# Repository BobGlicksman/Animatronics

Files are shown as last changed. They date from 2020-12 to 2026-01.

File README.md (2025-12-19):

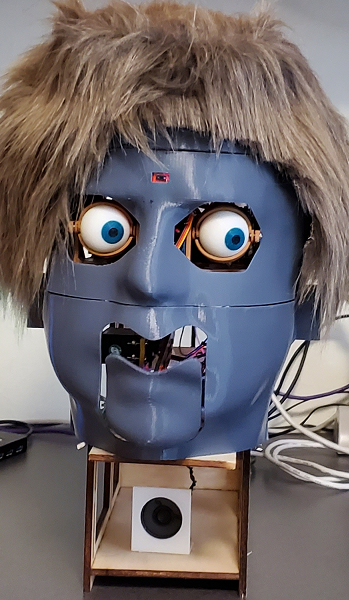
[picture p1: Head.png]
Head


# OVERVIEW.
This project developed an animatronic head.  The head is capable of detecting and tracking motion in its field of view and of controlling
an eye mechanism to "wake-up" and track this motion.  The head can also play various recorded voice clips and move its mouth to follow the 
audio in a "convincing manner".  The head can detect various events and select an appropriate voice clip to play in response to the event.

See the Overview document in the root folder of this repository for further details.

## Motivation.

This project was designed to explore various aspects of animatronics, including three specific technologies:

1. **TOF Sensor:**  The VL53L5CX intelligent sensor 
(https://www.sparkfun.com/sparkfun-qwiic-mini-tof-imager-vl53l5cx.html)
contains a matrix of SPAD diodes that detect the time-of-flight of infrared light
reflected off an object to compute the distance to that object.  The sensor can report out an 8 x 8 array of distance 
measurements up to 15 times per second, making it a "poor man's LIDAR".

2.  **Animatronic Eye Mechanism:**  We used an eye mechanism built from this project:
https://www.instructables.com/Simplified-3D-Printed-Animatronic-Dual-Eye-Mechani/ of Nilheim Mechatronics. 
They have a YouTube channel: https://goo.gl/7Cle6h. In June 2024, Will released a new version of the 3D files that 
snaps together - no screws! https://www.youtube.com/watch?v=uzPisRAmo2s.

3.  **Voice and Mouth Control:**  We use a DFPLayer Mini MP3 module from DFRobotics 
(https://www.dfrobot.com/product-1121.html?srsltid=AfmBOornrlH_d-dh73ndTnoJ0Bhm0fcPcsy0bjisI8v6idOF1iMq-ogo)
to play various audio clips that we recorded on a micro-SD card.  A custom-developed analog processing circuit
scales, filters and extracts the envelope from the audio signal and the sampled envelope undergoes further real-time
software digital signal processing in order to drive a mouth servo in a "convincing manner".

## R & D.

In order to best perform the R&D associated with this project, a laser cut skeleton was developed so that the electronics and servos
can be positioned flexibly.  The "head" itself is 3D printed and flexibly attached to the skeleton via 3D printed ears with magnets
glued onto the mounting ears and the head pieces.  All CAD files for the laser cut and 3D printed pieces are included in this repository.

### Eye Movement.

In order to explore using the complex eye mechanism to create realistic eye movement scenarios, a flexible software system was
developed.

1. **Scene:**  A "scene" is the combination of the movements of the 6 eye servos to produce some specific effect, e.g. blink the eyes.

2. **Scenario:**  A "scenario" is a timed script of various scenes that produce some overall effect, e.g. a "sleepy dog" whose eyes 
periodically open just a crack and the eyeballs move around to survey the landscape, and then the eyes close and the dog goes 
back to sleep.

Scenes and Scenarios can be easily custom-defined and combined to create a wide variety of overall eye motion effects.  In addition,
scenarios are defined and implemented to effect eye movement to realistically track motion detected by the TOF sensor.

### Voice and Mouth Movement.

The mouth control electronics can play pre-recorded MP3 voice clips under software command by the onboard microcontroller.
A custom-designed analog signal processing circuit provides the microcontroller's A/D converter with analog signals that 
it can sample and process digitally.

1. **Scaled audio:**  the left audio MP3 player channel is shifted and scaled to be within the microcontroller's A/D 
converter range of 0 - 3.3 volts.  The signal is also filtered to a 3.3 KHz bandwidth (telephone audio quality) so 
that the microcontroller can sample this signal at 8 KHz (> the Nyquist criteria) and perform whatever digital signal 
processing is desired (at 125 microseconds per sample).
The analog AC signal is offset for the single supply A/D converter and the zero-offset voltage is provided on another A/D converter input
so that this offset can be subtracted (in software) from each sample.  These inputs are provided by the hardware but are not used
in the currently released software.

2. **Envelope Extraction:**  The scaled audio signal is further processed to extract the "envelope" of the audio signal by AM demodulation.
The bandwidth of the extracted envelope signal is approximately 40 Hz, which was empirically determined to preserve the full
information about the vocal elements of the voice clip while rejecting the "carrier" frequencies.  The envelope signal is 
connected to a 3rd A/D converter channel and the software samples this at 100 Hz.

The sampled envelope signal is processed in software to control the mouth servo.  In order to explore the nuances of controlling
the mouth servo to be "convincing", various configurable processing stages are provided in the released software:

a. **Linear and non-linear processing:**  The input envelope samples are scaled using either a linear or a non-linear scaling
algorithm.  The released software is configured for linear scaling, but realistic non-linear algorithms may be explored in
the future.

b. **Averaging:**  The 40 Hz envelope bandwidth and 100 Hz sampling are currently used to drive the mouth servo.  However,
1 to 5 samples may be averaged before being mapped to the servo drive.  The servo that we are using seems to work best
when driven without averaging the samples, and extreme averaging creates a noticeable lag between the audio and mouth movements.
However, averaging may be useful with other mechanical mouth linkages.

c.  **Servo scaling:** the processed samples are scaled to the desired servo range of travel before being used to control the mouth
servo.

### TOF Sensor.

The TOF sensor is very sophisticated and required a substantial amount of experimentation before we could use it successfully.
After figuring out what all of the controllable parameters do and how best to set them, we then worked on the actual application
of the sensor to this project.  The application includes:

1.  **Calibrating the room:**  Upon powering up the head, the room should be empty.  The software records the distance measurements
for the empty room so that it can later determine if anything has entered the room and respond to it.

2.  **Tracking movement:**  Tracking movement within the sensor's field of view turned out to be a challenge, as an 8 x 8 matrix of
distance measurements is complex.  In order to fix a point in space that is closet to the sensor, we had to combine both
spatial and temporal filters to reject "noise" in the data.  This filtering was necessary to produce non-jittery positioning
of the eyes to focus on the closest subject area in space.

3.  **Event detection:**  The software further processes the TOF data in order to detect various "events" for the head to
respond to:  (a) person(s) entering the TOF field of view, (b) person(s) leaving the TOF field of view, (c) person(s)
coming too close to the head.  Other events might be explored in the future.

# WHAT IS IN THIS REPOSITORY.

## Top Level.

1.  This README file.

2.  A photo of the Head.

3.  An Overview document describing this project in more detail.

4.  License information.

## Data Folder.

This folder contains digitized audio test files that were used with analysis and circuit simulation software to develop the analog
signal processing parameters for the circuit design.  These files are preserved for historical purposes and for further research;
they are not needed to implement the current animatronic head design.

## Documents Folder.

This folder contains the documentation for this project including several documents that detail the design, construction and operation of this project.

## Hardware Folder.

This folder contains information about the electronic design, including PCB CAD files and hookup data

## Legacy Folder.

This folder contains source code for various test programs that were used to exercise and research the various components
of the animatronic head prior to integrating the complete project.  These files are not part of the released head design but
are retained for possible use in future R&D.

## Mechanical Folder.

This folder contains the 2D and 3D CAD files for the skeleton, the head, the eye mechanism and other 3D printed mechanical
components of this project.

## Software Folder.

This folder contains source code for the two Particle Photon 1 microcontrollers used on this project.  The source code includes
the released operational code for each of the Photons, as well as some test and calibration code that needs to be used for
construction and calibration of the animatronic head.

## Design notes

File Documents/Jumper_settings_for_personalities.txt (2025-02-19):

JUMPER SETTINGS FOR PERSONALITIES

A5 = MSB; A4 = LSB; Logic is positive (open pin = 1, grounded pin = 0

Bob Personality #1:  ground both A4 and A5
Bob Personality #2 (not yet implemented): Ground A5, Open A4
Jim Personality #1: Open A5, Ground A4
Jim Personality #2 (not yet implemented): Open A5, Open A4

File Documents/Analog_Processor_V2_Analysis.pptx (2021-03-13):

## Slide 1

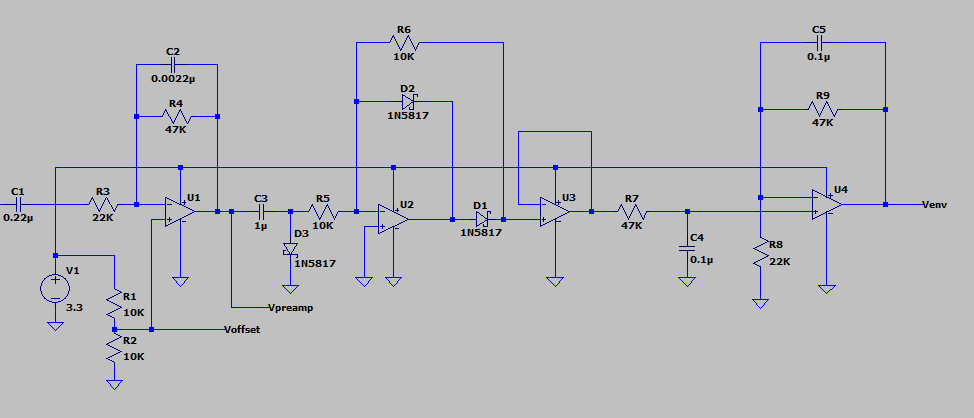
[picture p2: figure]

Op-Amps are OPA4342
- Quad opamp
- Single Supply
- Rail-Rail
- FET

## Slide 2

Input Filter/Preamp

Rectifier

Vpreamp

Voffset

Buffer

Envelope Filter

Audio
Input

Venv

Env Filter:
- Envelope filter (~0Hz – 40Hz)
- ~ 2x Gain

Pre-amp:
- Audio filter (~3Hz – 3KHz)
- DC offset (50% Vsupply)
- ~2x Gain

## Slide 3

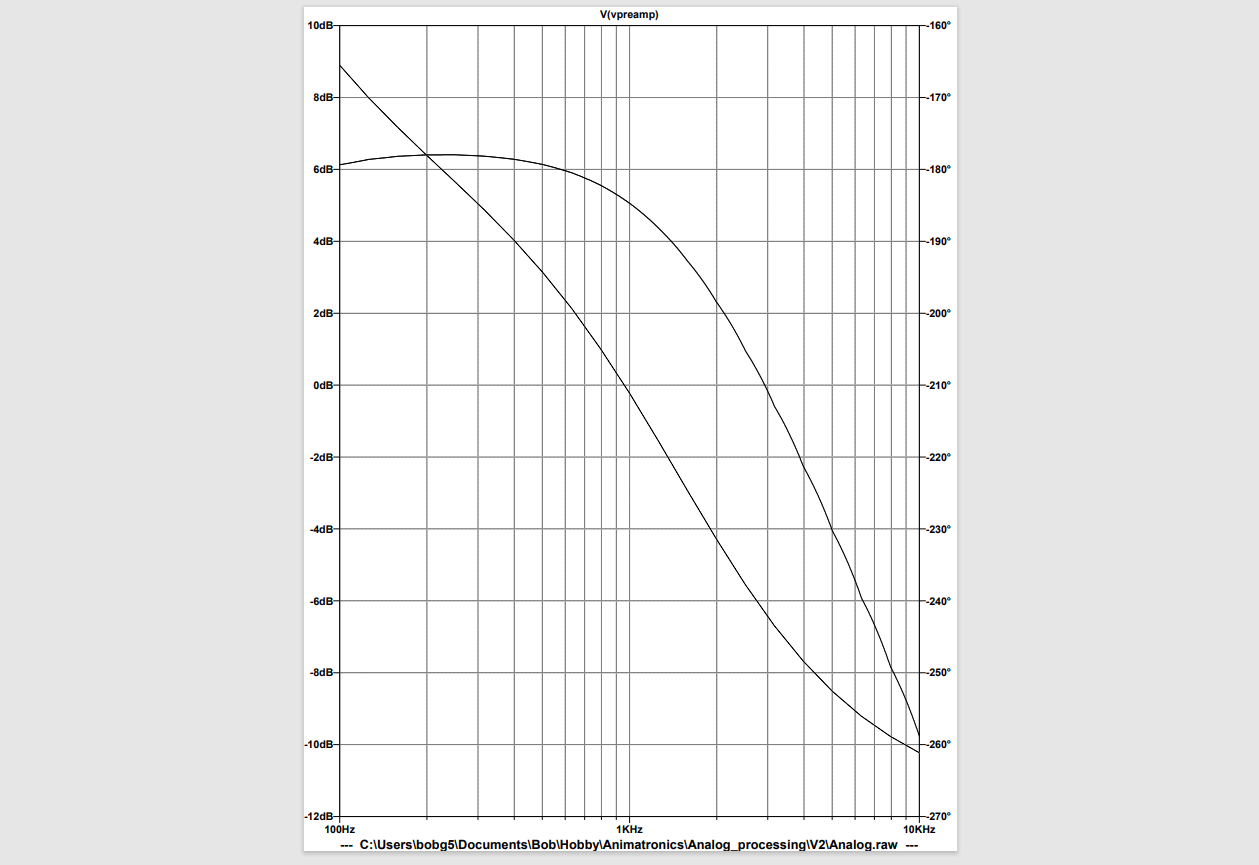
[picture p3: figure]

Frequency

Phase

Preamplifier
Frequency Response

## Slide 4

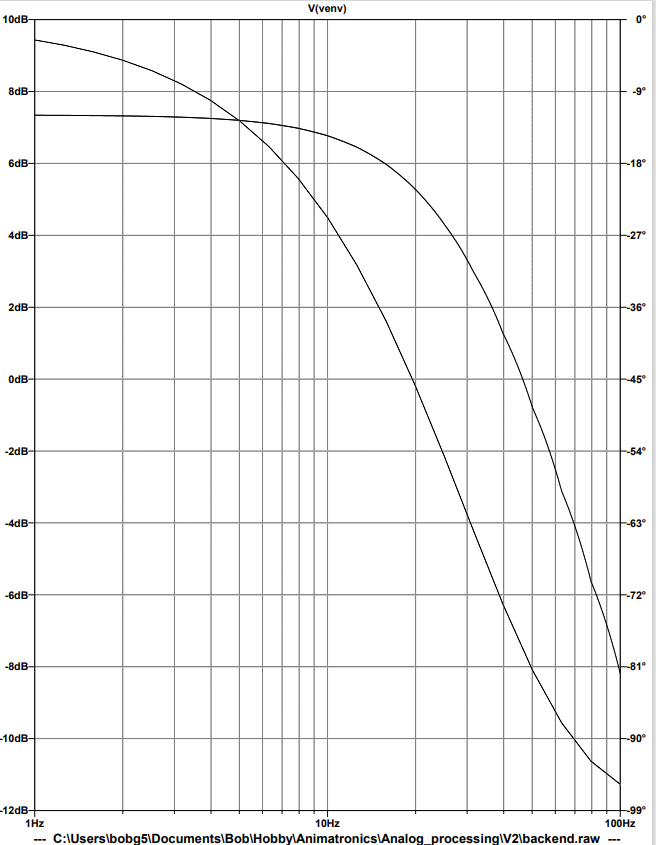
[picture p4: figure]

Frequency

Envelope Filter
Frequency Response

Phase

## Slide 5

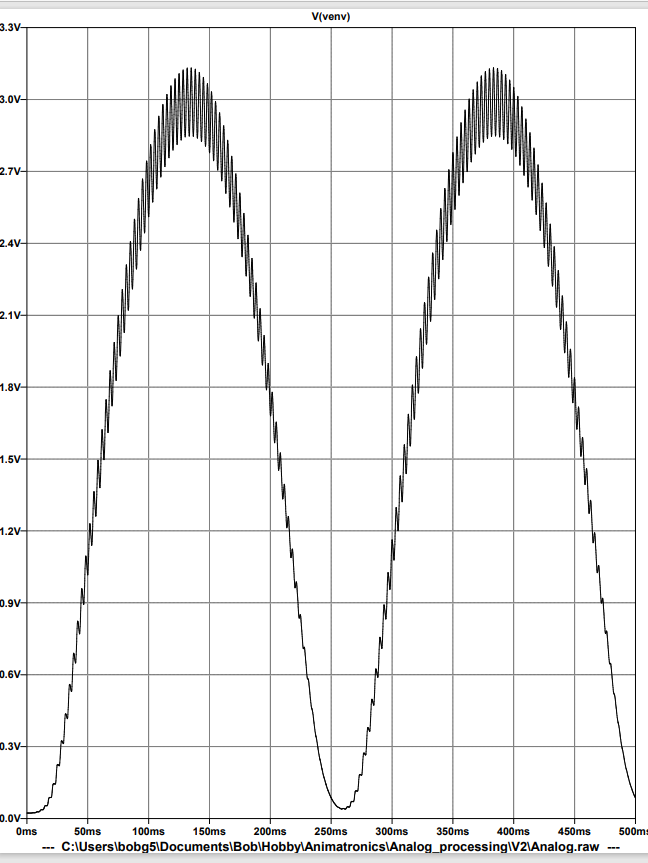
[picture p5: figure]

Carrier = 300 Hz
Modulation = 2 Hz

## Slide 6

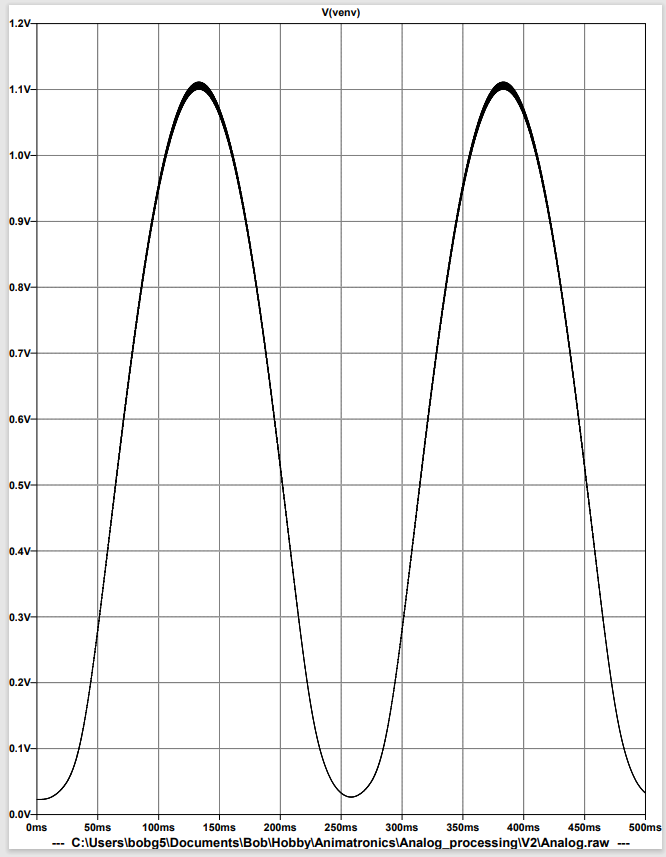
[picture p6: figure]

Carrier = 3000 Hz
Modulation = 2 Hz

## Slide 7

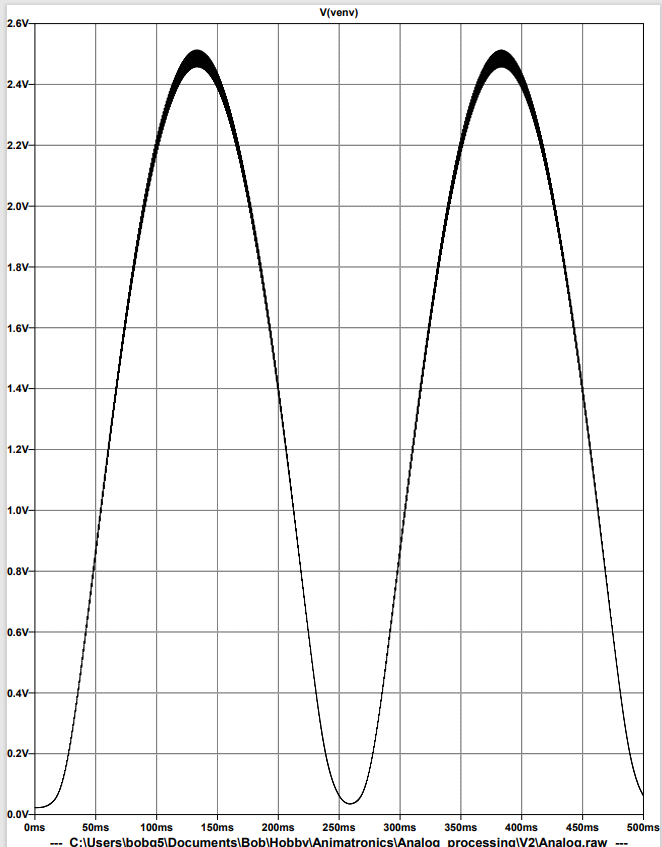
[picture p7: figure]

Carrier = 1200 Hz
Modulation = 2 Hz

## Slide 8

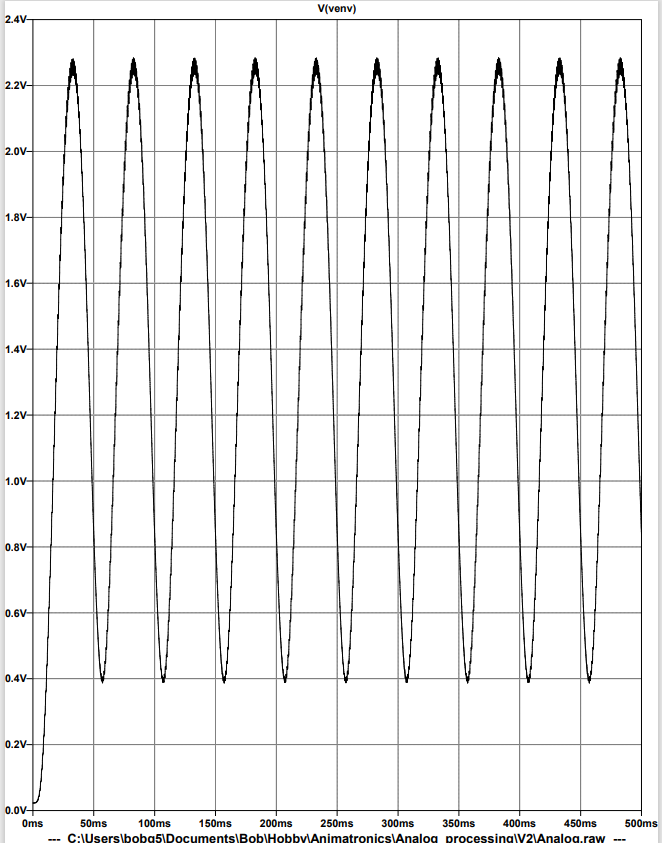
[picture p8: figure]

Carrier = 1200 Hz
Modulation = 10 Hz

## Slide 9

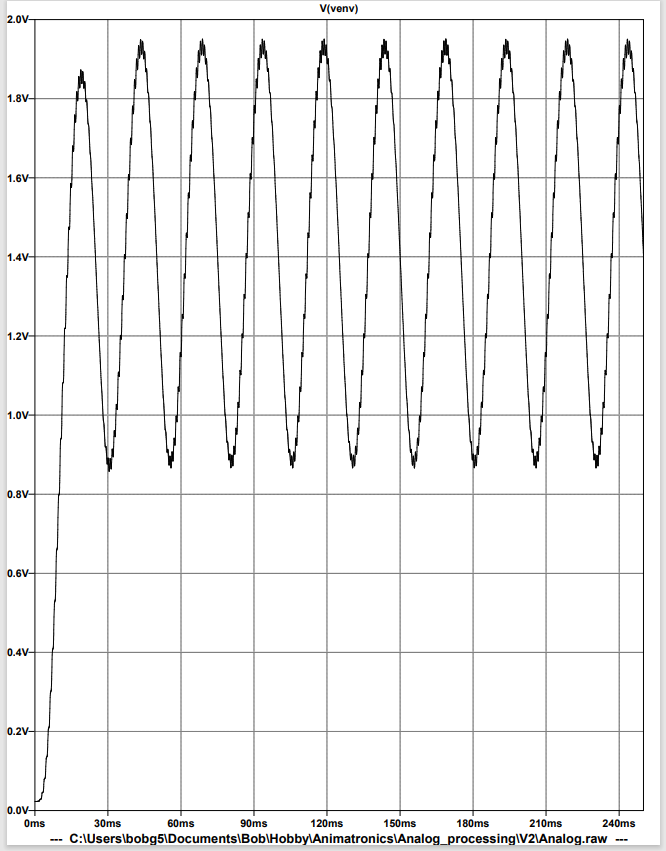
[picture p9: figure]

Carrier = 1200 Hz
Modulation = 20 Hz

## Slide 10

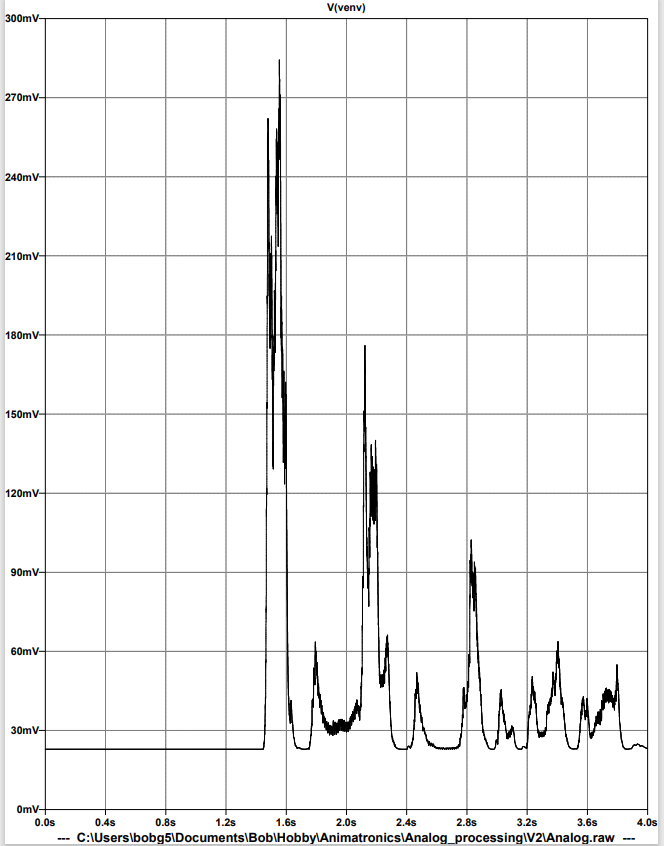
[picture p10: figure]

Welcome.wav

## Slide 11

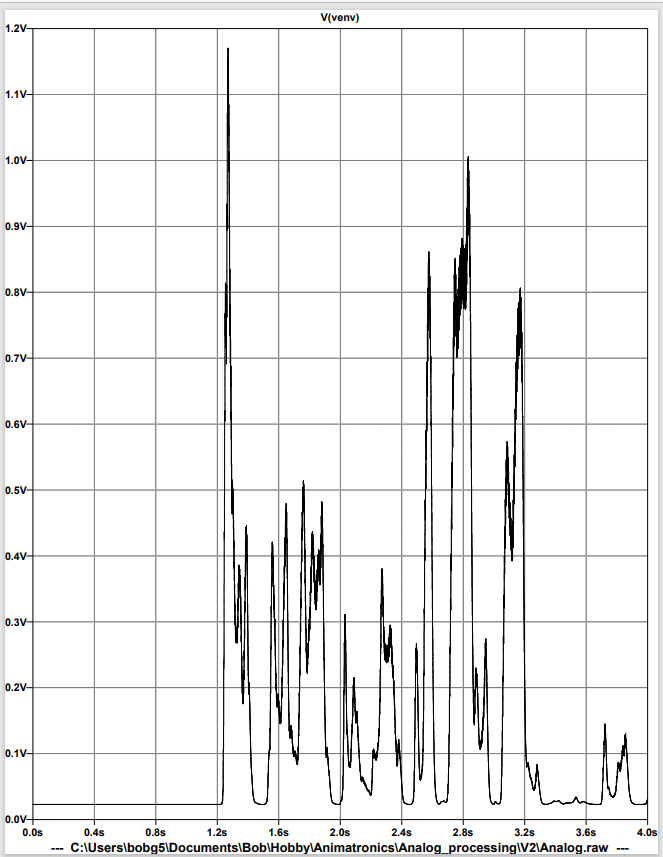
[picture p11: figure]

Welcome_high.wav

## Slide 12

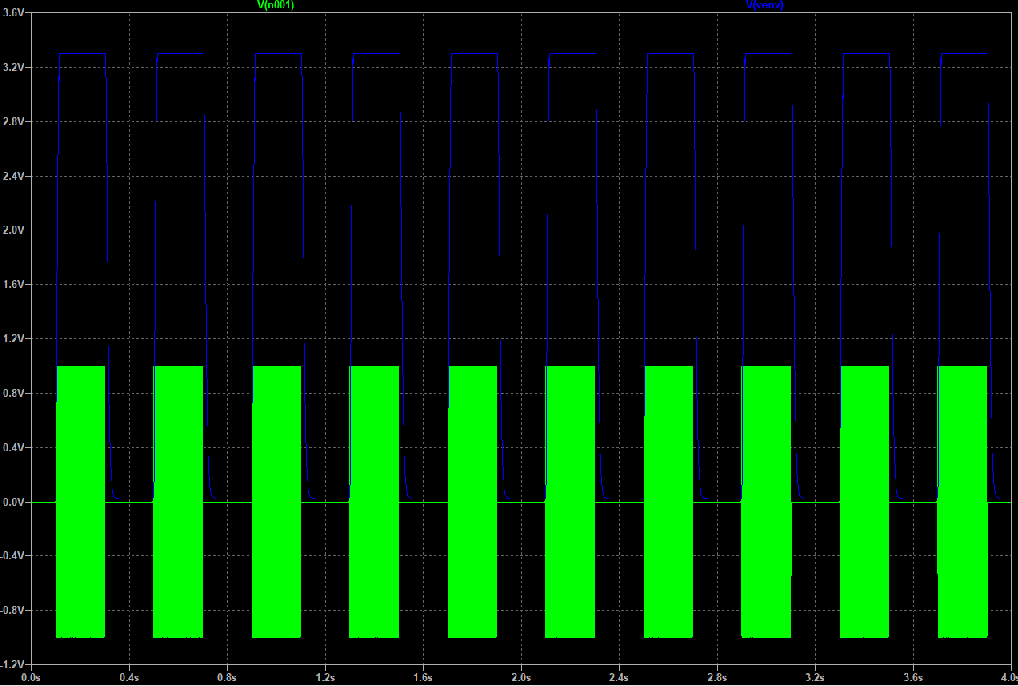
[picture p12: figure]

Pulse_1000_20.wav

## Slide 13

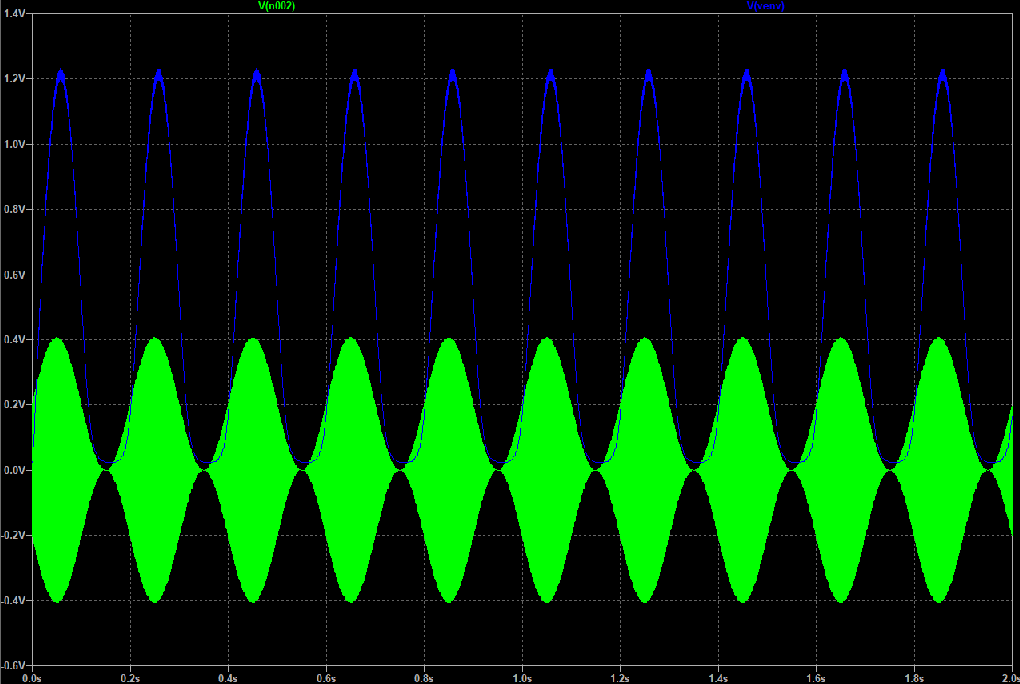
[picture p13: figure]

sin_1000_5.wav

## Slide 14

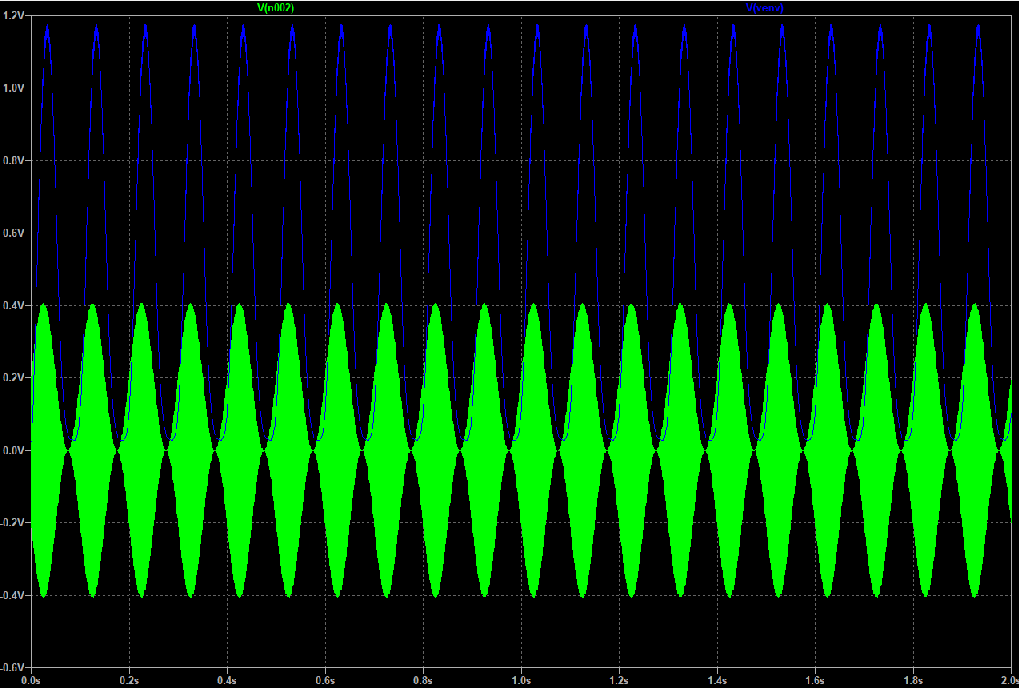
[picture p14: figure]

sin_1000_10.wav

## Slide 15

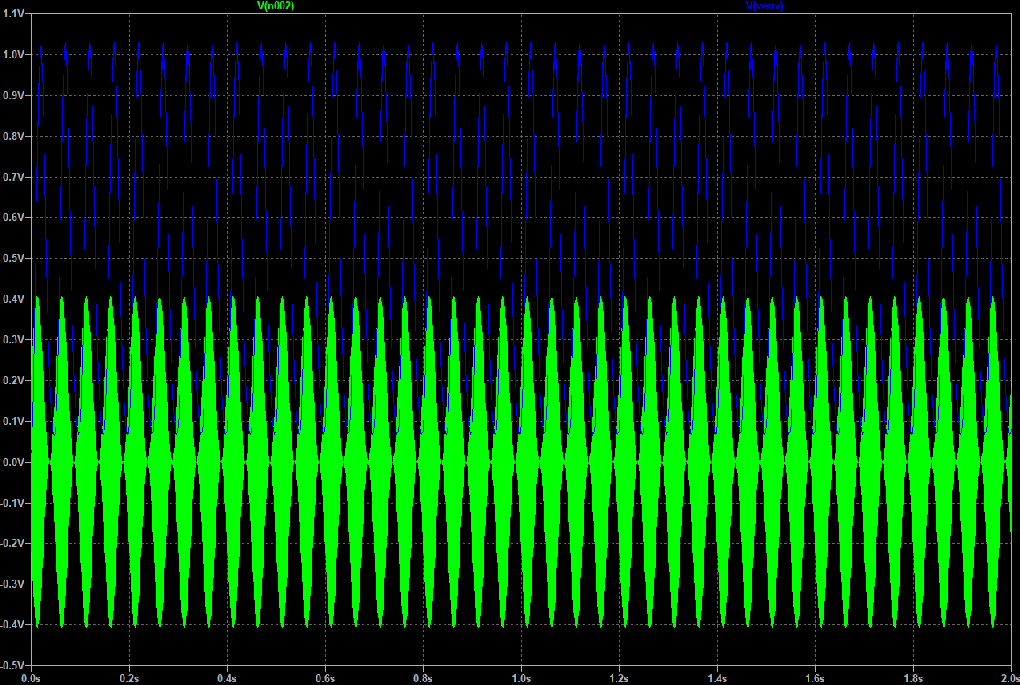
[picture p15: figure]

sin_1000_20.wav

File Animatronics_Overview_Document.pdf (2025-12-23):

# Animatronics Overview Document

By: Jim Schrempp and Bob Glicksman; v1.1, 12/23/2025

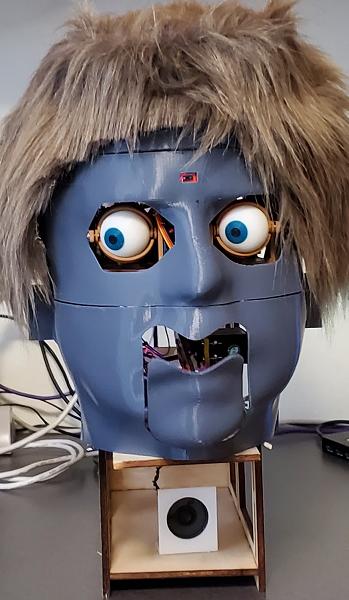
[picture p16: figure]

© 2025 Team Practical Projects, Bob Glicksman, and Jim Schrempp. All rights reserved.

NOTICE: Use of this document is subject to the terms of use described in the document
“Terms_of_Use_License_and_Disclai mer” that is included in this release package. This document can be found at:

https://github.com/TeamPracticalProjects/Animatronics/blob/main/Terms_of_Use_License_and_Disclaimer.pdf

© 2025, Team Practical Projects, Jim Schrempp and Bob Glicksman; all rights reserved. Subject to “Terms of Use, License and Disclosure”

TABLE OF CONTENTS.

TABLE OF CONTENTS. | 0
DOCUMENT OVERVIEW. | 2
PROJECT DESCRIPTION. | 2
Project Overview. | 2
The Structure. | 3
The Brain. | 6
The Eyes. | 7
The Mouth. | 9
DOCUMENTATION TREE. | 10
Animatronic Head Structural-Mechanical Hardware Document. | 11
Animatronic Head Electronic Hardware Document. | 11
Animatronic Brain Document. | 11
Animatronic Head Eye Mechanism Document. | 11
Animatronics Mouth Software Description Document. | 12
Analog Processor V2 Analysis. | 12
Jumper Settings for Personalities. | 12
CONTENTS OF THIS REPOSITORY. | 13
Root. | 13
Data. | 13
Documents. | 13
Hardware. | 13
Legacy-NotPartOfRelease. | 14
Mechanical. | 14
Software/Photonfirmware. | 14
https://github.com/TeamPracticalProjects/Animatronics/tree/main/Software/Photonfirmw
are/AnimatronicEyesCalibration | 14
https://github.com/TeamPracticalProjects/Animatronics/tree/main/Software/Photonfirmw
are/AnimatronicEyesTest | 14
https://github.com/TeamPracticalProjects/Animatronics/tree/main/Software/Photonfirmware/
AnimatronicMouthDemo | 15

DOCUMENT OVERVIEW.

This document provides an overview of the Team Practical Projects’ Animatronic Head project. The Animatronic Head is a complex project. A complete description of this project is contained in a number of documents, each detailing a specific aspect of the design. This document contains a high level overview of the project and should be the “first read” document serving as an introductory overview of the project.

PROJECT DESCRIPTION.

Project Overview.

The Animatronic Head project was designed and developed to explore various aspects of animatronic interaction with humans. The Animatronic Head (Head) consists of:

- A “Brain”. An 8x8 matrix Time-of-Flight (TOF) sensor provides the Head with a crude, three dimensional view of its nearby surroundings. “Brain” software processes this information to determine when a visitor is inside of its relevant field of view and what the visitor is doing, so that the Head can interact with him/her.
- The “Eyes”. A six servo eye mechanism provides complex movements of an animatronic set of eyes. The mechanism allows independent software control of upper and lower eyelids on each eye as well as coordinated vertical and horizontal movement of the left and right eyeballs. The software has been designed in a programmable, hierarchical manner that provides an infrastructure to experiment with complex and interactive eye movement scenarios.
- The “Mouth”. A simple, single servo mechanism moves the jaw to simulate mouth movements when speaking. The “Mouth” electronics can play pre-recorded MP3 voice clips though a small loudspeaker. On-board analog signal processing circuitry extracts the “envelope” of the spoken voice clip and software digital processing of this envelope waveform moves the “Mouth” servo in synchronism with the audio in order to create the illusion that the Head is speaking to the visitor.

The overall structural and mechanical design of the Animatronic Head was developed with experimentation and iteration in mind. Separate microcontroller-based electronics are provided for the “Brain/Eyes” and for the “Mouth” so that these components can be developed and experimented with independently. These two electronic elements are interconnected by a

Particle¹ Cloud-based publish/subscribe mechanism that allows the entire project to be interconnected and synchronized while still being extensible for future experimentation and use.

The Structure.

In order to make this project suitable for experimentation and evolution, a flexible frame was created in 2D CAD and the pieces cut out on a laser cutter. The basic frame structure is shown in figure 1.

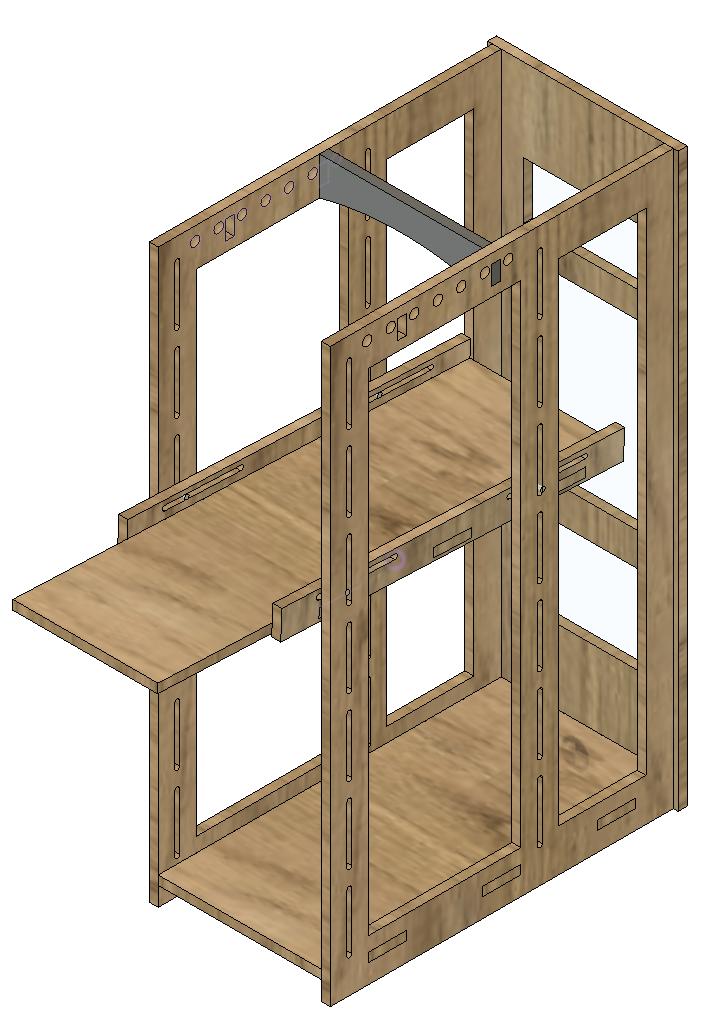
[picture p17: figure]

Figure 1. Frame Design.

Figure 2 provides a side overview of the assembled project. Two identical sides, a base, a back and a top handle are glued together to form a rigid, yet open frame that mounts all of the mechanical and electronic components. Two shelves are used to mount the major electronic and mechanical components. The shelves can be mounted at adjustable heights in order to precisely align the mechanisms with the 3D printed face. Adjustment is provided using screws and wingnuts.

1 Particle.io

The 3D printed face consists of a crown, the eyes, and the mouth. Each of these 3D printed face pieces is mounted to the frame using magnets that are glued to 3D printed mounting ears and to the back of the face piece. The mounting ears can be flexibly placed on the frame using screws and wingnuts.

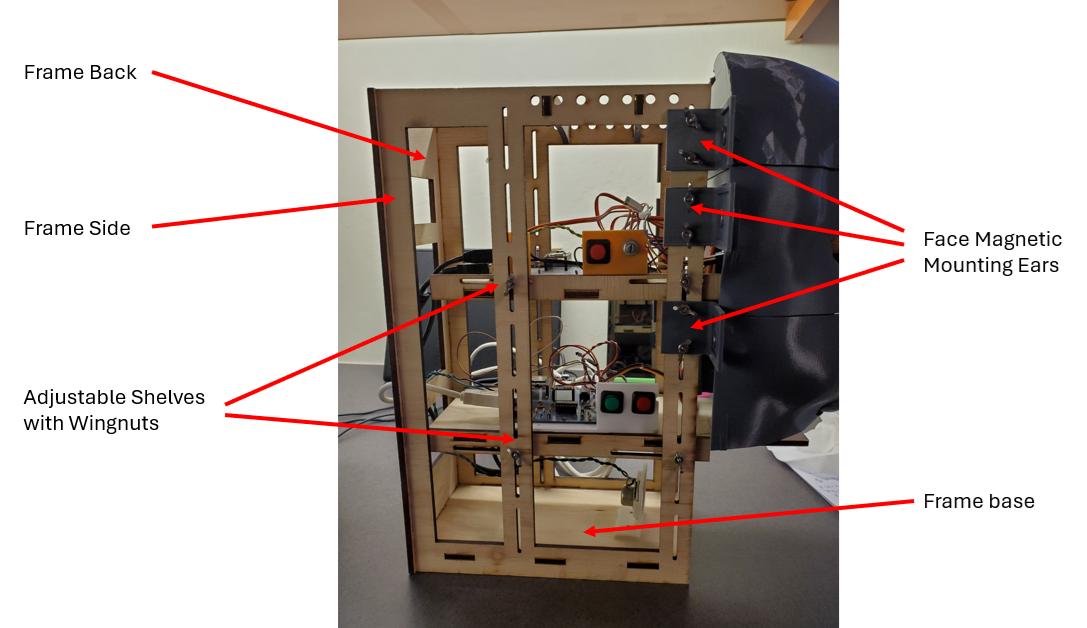
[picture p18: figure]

Figure 2. Frame Fully Assembled.

The upper shelf holds the 3D printed eye mechanism, an electronic servo control board, and a custom printed circuit board that holds a Particle Photon 1 microcontroller. The second, lower shelf holds the Mouth mechanism and mouth electronics printed circuit board. The mouth printed circuit board also uses a Particle Photon 1 microcontroller and provides the MP3 audio player module and custom designed analog signal processing circuitry. See figures 3 and 4 for a close-up view of these components.

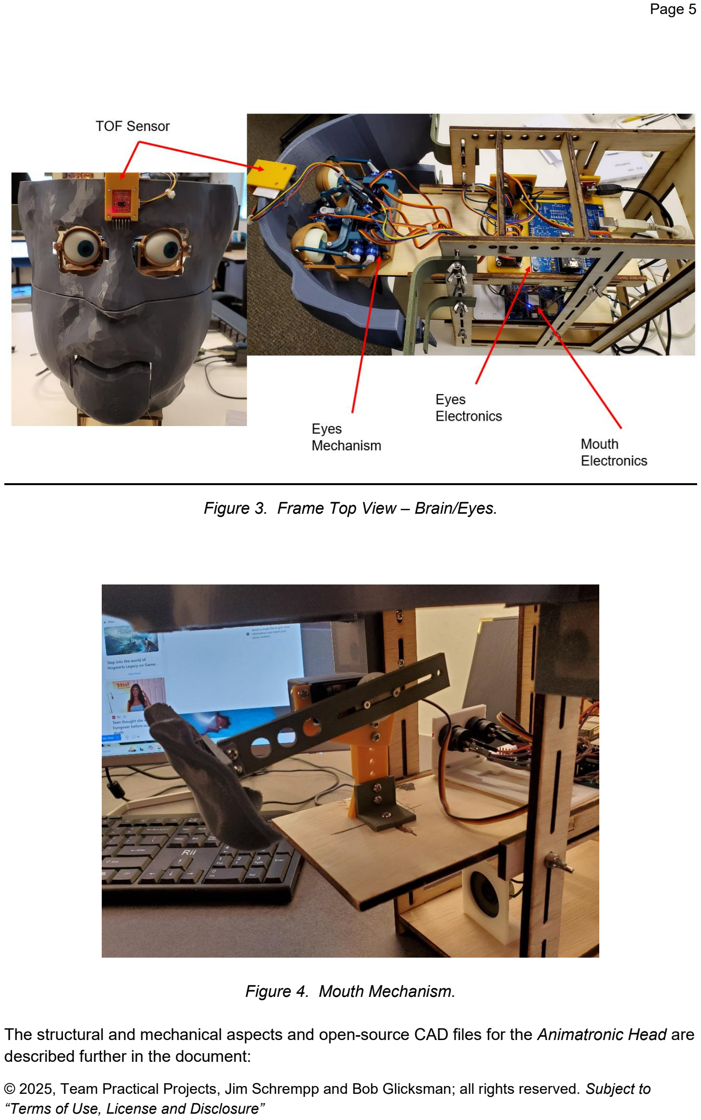
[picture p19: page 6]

Figure 3. Frame Top View – Brain/Eyes.

Figure 4. Mouth Mechanism.

The structural and mechanical aspects and open-source CAD files for the Animatronic Head are described further in the document:

https://github.com/TeamPracticalProjects/Animatronics/blob/main/Documents/Animatronic%20H ead%20Structural-Mechanical%20Hardware%20Document.pdf (https://github.com/TeamPracticalProjects/Animatronics/blob/main/Documents/Animatronic%20Head%20Structural-Mechanical%20Hardware%20Document.pdf)

The Brain.

The “Brain” of the Animatronic Head uses an 8 x 8 matrix optical time-of-flight (TOF) sensor to gather information about the environment:

https://www.sparkfun.com/sparkfun-qwiic-mini-tof-imager-vl53l5cx.html

A larger but easier to experiment with version of the same sensor can also be used:

https://www.sparkfun.com/sparkfun-qwiic-tof-imager-vl53l5cx.html

Both of these modules use a VL53L5CX TOF sensor from ST Electronics. Each sensor of the 8 x 8 sensor array provides a precise distance measurement to a corresponding object within the sensor’s field of view. The VL53L5CX can provide a new 8 x 8 frame of measurement data up to 15 times per second, over an I2C (Qwiic) bus connection. Connection of the Photon 1 microcontroller custom printed circuit board (PCB) to a 16 channel servo control board and to this sensor is shown in figure 5, below.

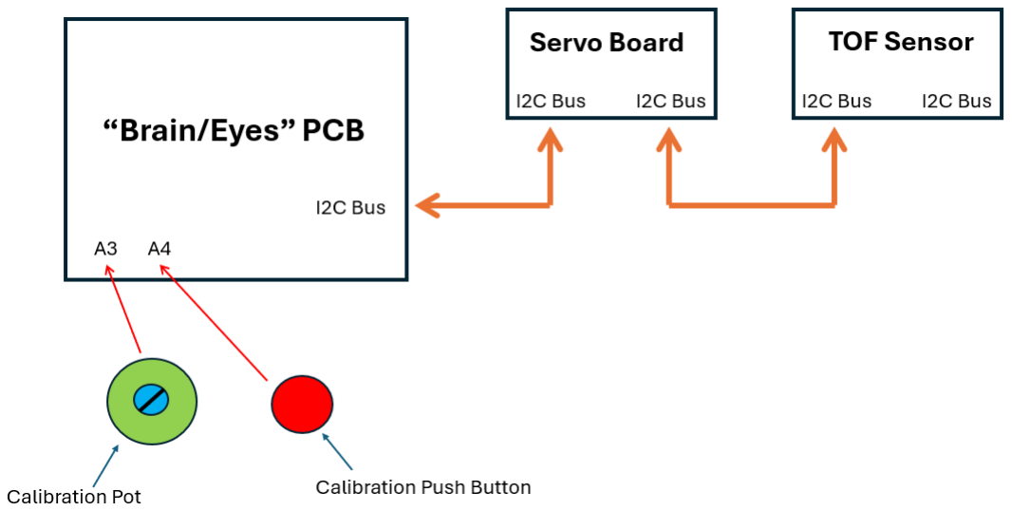
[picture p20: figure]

Figure 5. Brain/Eyes Electronics.

Software on the “Brain/Eyes” microcontroller reads frames of sensor data continuously. When the electronics are initialized, the sensor “scene” is calibrated for an empty room. This calibration provides a “picture” of the empty room – where static “background” objects are located, so that future human movement in front of these objects can be determined. The calibration also limits the scope of the sensor “Brain” processing to approximately 2 meters in front of the Head. The Brain will not respond to anything further away than this.

Experimentation with this sensor has shown that its output is “noisy”. Both background optical noise and multi-path “noise” seem to be the culprits. In order for the “Brain” to determine what is inside of its sensing envelope and what is closest to the Head, both spatial and temporal processing filters are applied (in software) to the regular frames of data from the sensor.

Filtered frames of distance measurements from the sensor are processed (in software) to determine the center point of whatever is closest to the Head inside of its field of view, but in front of its “empty room” calibration. This information is used to move the eyes so that they track a visitor who enters the Head’s field of view. The brain software also processes this information to publish various “events” of significance to the Particle Cloud:

- Person first enters the field of view.
- Person approaches the Head too closely
- Person leaves the field of view after engagement with the Head
- Person leaves the field of view too soon after arrival (too soon for engagement with the Head).

These events are subscribed to by the “Eyes” Photon 1 processor and are used to play appropriate audio clips over the Mouth loudspeaker.

The “Brain” processing, and how it moves the “Eyes”, is further described in the document:

https://github.com/TeamPracticalProjects/Animatronics/blob/main/Documents/Animatronics%20 Brain%20Document.pdf (https://github.com/TeamPracticalProjects/Animatronics/blob/main/Documents/Animatronics%20Brain%20Document.pdf)

The electronic hardware used on the Head is further described in the document:

https://github.com/TeamPracticalProjects/Animatronics/blob/main/Documents/Animatronic%20H ead%20Electronic%20Hardware%20Document.pdf (https://github.com/TeamPracticalProjects/Animatronics/blob/main/Documents/Animatronic%20Head%20Electronic%20Hardware%20Document.pdf)

The Eyes.

The eyes mechanism itself is an intricate assembly consisting of six hobby servos and an integrated set of 3D printed parts. We adapted the following excellent mechanism from Will Cogly’s design on the Internet; see:

https://www.instructables.com/Simplified-3D-Printed-Animatronic-Dual-Eye-Mechani/

The maker, Will Cogley, is incredibly inventive. His YouTube channel has a lot of amazing things:

https://www.youtube.com/channel/UCkUD_8b1JoTL2ipOVtxfNKw

We modified a few of the eye mechanism parts, see:

https://github.com/TeamPracticalProjects/Animatronics/tree/main/Mechanical/EyeMech

Owing to pin limitations on the Photon 1 microcontroller, we used an external 16 channel servo module to control the 6 servos of this eye mechanism; see:

https://www.adafruit.com/product/815

This module connects to the “Brain/Eyes” PCB using the I2C bus; see figure 5, above.

The “Brain/Eyes” Photon 1 software has been designed for experimentation with eye movement effects. To this extent, a “software stack” has been developed that provides a hierarchical means of creating complex eye movements:

- Basic movements of each servo: position and speed of movement to a new position are encapsulated into objects of the animateServo class.
- Coordinated movements of various servos into a scene (e.g. blink the eyes) incorporate animateServo objects into instances of the animatePuppet class.
- Time sequenced lists of animatePuppet objects create complex scenarios; e.g. a “sleepy dog” effect whose eyes are normally closed, then open halfway, the eyes pan left/right to survey the scene, and then close again when the dog goes back to sleep.

These eye movement effects can be “standalone” or linked to “Brain” object tracking information. Both of these effect types are incorporated into the “Brain/Eye” software that is released as part of this project. See the following document for further information:

https://github.com/TeamPracticalProjects/Animatronics/blob/main/Documents/Animatronics%20 Brain%20Document.pdf (https://github.com/TeamPracticalProjects/Animatronics/blob/main/Documents/Animatronics%20Brain%20Document.pdf)

The complex eye system requires calibration after the 3D printed mechanism is assembled. Special calibration software guides the user through the calibration process, using a potentiometer and pushbutton that are connected to the electronics PCB as shown in figure 5. A detailed description of the eyes control and the calibration process in the following document:

https://github.com/TeamPracticalProjects/Animatronics/blob/main/Documents/Animatronic%20H ead%20Eye%20Mechanism%20Document.pdf (https://github.com/TeamPracticalProjects/Animatronics/blob/main/Documents/Animatronic%20Head%20Eye%20Mechanism%20Document.pdf)

The Mouth.

The “Mouth” PCB contains a DFRobot DFPlayer mini MP3 player module:

https://www.dfrobot.com/product-1121.html

This module accepts a micro SD card and can play MP3 format audio clips through a small loudspeaker. Software on a Particle Photon 1 microcontroller on the “Mouth” PCB controls which clip to play in response to events that it subscribes to via the Particle Cloud. In the Animatronic Head project, these events are published by the “Brain/Eyes” electronics. However, the “Mouth” electronics are otherwise independent and can be deployed separately on other projects.

Connections to the “Mouth” PCB are shown in figure 6. In addition to the Photon 1 and the mini MP3 player, the “Mouth” PCB contains custom designed analog signal processing circuitry. This circuitry conditions the analog signal output from the mini MP3 player and then extracts the “envelope” of the signal via AM demodulation. The envelope signal is bandlimited to about 40 Hz and then sampled by the Photon 1 A/D converter every 10 milliseconds²

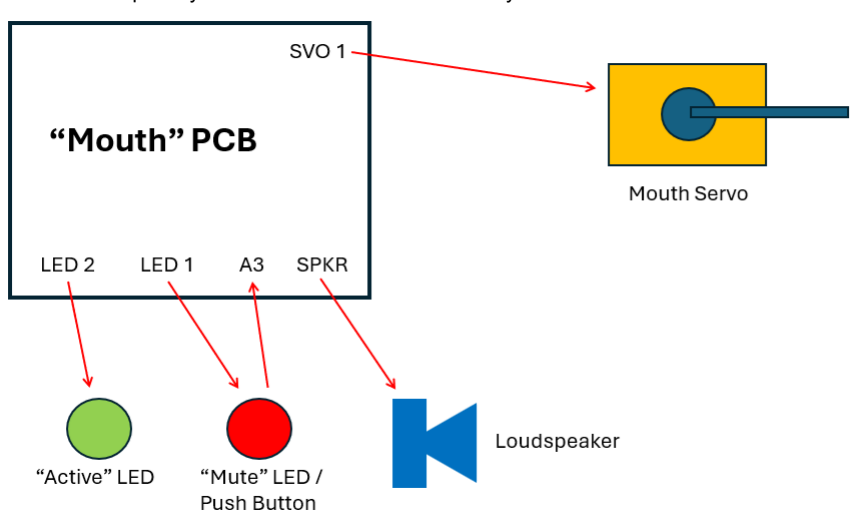
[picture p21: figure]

Figure 6. Mouth Electronics.

2 This 100 Hz sampling rate exceeds the Nyquist criterion for the 40 Hz bandlimited envelope signal.

These analog/digital samples are then processed in software through a digital signal processing chain that ultimately drives the servo that moves the mouth in synchronism with the audio clip being played. The digital signal processing chain is designed to allow for experimentation toward providing the most convincing movement of the “Mouth”.

The “Mouth” electronics and the theory of operation of the analog signal processing circuitry are described further in the document:

https://github.com/TeamPracticalProjects/Animatronics/blob/main/Documents/Animatronic%20H ead%20Electronic%20Hardware%20Document.pdf (https://github.com/TeamPracticalProjects/Animatronics/blob/main/Documents/Animatronic%20Head%20Electronic%20Hardware%20Document.pdf)

The Photon 1 software contains tools for experimenting with settings for the software digital processing chain. The user can interact with these settings using the Particle Console. The best settings for presentation of each pre-recorded voice clip are stored with the software in an included file. When clips are triggered to be played back, they are then played with optimal volume and mouth movement settings.

The “Mouth” software allows several “personalities” to be used with the Head. Each “personality” contains a set of one or more audio clips that are associated with a given Cloud event. When an event is received from the Cloud, a clip for that event within the selected “personality” is randomly chosen for playback. This mechanism allows the Head to be set up to play different clips in different voices depending upon the venue where the Head is being demonstrated.

A detailed description of the “Mouth” software, along with instructions for optimizing the processing chain for each recorded clip, is found in the document:

https://github.com/TeamPracticalProjects/Animatronics/blob/main/Documents/Animatronics_Mouth_Software_Description_Document.pdf (https://github.com/TeamPracticalProjects/Animatronics/blob/main/Documents/Animatronics_Mouth_Software_Description_Document.pdf)

DOCUMENTATION TREE.

The Animatronic Head is a complex project. This Overview document only summarizes the technical aspects of the project. The Documents folder contains additional, more detailed descriptions of the structural, mechanical, electronic and software elements of the project. This section describes each of the files in the Documents folder. Many of these documents have been referenced earlier in this Overview.

Animatronic Head Structural-Mechanical Hardware Document.

https://github.com/TeamPracticalProjects/Animatronics/blob/main/Documents/Animatronic%20H ead%20Structural-Mechanical%20Hardware%20Document.pdf (https://github.com/TeamPracticalProjects/Animatronics/blob/main/Documents/Animatronic%20Head%20Structural-Mechanical%20Hardware%20Document.pdf)

This document contains details of the overall structural and mechanical elements of the Animatronic Head. It contains detailed photos and drawings of the physical and mechanical aspects of the project. It also provides references to the CAD source files that are in the Mechanical folder in this repository.

Animatronic Head Electronic Hardware Document.

https://github.com/TeamPracticalProjects/Animatronics/blob/main/Documents/Animatronic%20H ead%20Electronic%20Hardware%20Document.pdf (https://github.com/TeamPracticalProjects/Animatronics/blob/main/Documents/Animatronic%20Head%20Electronic%20Hardware%20Document.pdf)

This document contains detailed descriptions of the electronic components and electronic interconnections of both the “Brain/Eye” electronic subsystem and the “Mouth” electronic subsystem. It describes the electronic design, theory of operation, and assembly of the custom electronic printed circuit boards used on this project and the interconnection of external modules and components to these circuit boards. It contains links to the open source electronic CAD and software files that are provided in this repository (in the Hardware and Software folders, respectively).

Animatronic Brain Document.

https://github.com/TeamPracticalProjects/Animatronics/blob/main/Documents/Animatronics%20 Brain%20Document.pdf (https://github.com/TeamPracticalProjects/Animatronics/blob/main/Documents/Animatronics%20Brain%20Document.pdf)

This document provides a detailed description of the algorithms used to process data from the optical time-of-flight (TOF) sensor: determination and tracking of the closest object in its field of view and the generating of the events that are published to the Particle Cloud. It provides a detailed description of the hierarchical software structure that allows development of, and experimentation with, complex coordinated eye movements and effects. The document contains links to the open source software files that are provided in this repository (in the Software folder).

Animatronic Head Eye Mechanism Document.

https://github.com/TeamPracticalProjects/Animatronics/blob/main/Documents/Animatronic%20H ead%20Eye%20Mechanism%20Document.pdf (https://github.com/TeamPracticalProjects/Animatronics/blob/main/Documents/Animatronic%20Head%20Eye%20Mechanism%20Document.pdf)

This document provides a detailed description of the calibration and control of the complex, six servo eye mechanism. It guides the user through the special calibration procedure and software needed to calibrate a newly assembled mechanism and describes how to incorporate the calibration data into the “Brain” software. The document contains links to the open source software files that are provided in this repository (in the Software folder).

Animatronics Mouth Software Description Document.

https://github.com/TeamPracticalProjects/Animatronics/blob/main/Documents/Animatronics_Mouth_Software_Description_Document.pdf (https://github.com/TeamPracticalProjects/Animatronics/blob/main/Documents/Animatronics_Mouth_Software_Description_Document.pdf)

This document provides a detailed description of the digital software algorithms used to process sampled envelope data from the “Mouth” electronics hardware into movements of the mouth servo. It provides instructions for setting and monitoring the various processing settings that are available for experimentation with optimizing the mouth movement effects. The document contains links to the open source software files that are provided in this repository (in the Software folder).

Analog Processor V2 Analysis.

https://github.com/TeamPracticalProjects/Animatronics/blob/main/Documents/Analog_Processor_V2_Analysis.pptx (https://github.com/TeamPracticalProjects/Animatronics/blob/main/Documents/Analog_Processor_V2_Analysis.pptx)

This document is a PowerPoint slide deck that details the results of the design and simulation of the “Mouth” electronics analog signal processing circuitry. The simulation used LTSpice to provide time and frequency/phase domain data on a number of test data files that were created to verify the analog circuit design. The resulting waveforms are presented along with the wave files that were created to drive the simulated circuit in LTSpice. The audio test files themselves are included in the Data folder in this repository.

Jumper Settings for Personalities.

https://github.com/TeamPracticalProjects/Animatronics/blob/main/Documents/Jumper_settings_for_personalities.txt (https://github.com/TeamPracticalProjects/Animatronics/blob/main/Documents/Jumper_settings_for_personalities.txt)

This very brief document lists the jumper settings for the “Mouth” personalities that are released in the Software and Data files in this repository.

CONTENTS OF THIS REPOSITORY.

The folder structure and contents of this GitHub repository are described in this section.

Root.

The Root folder contains this Overview document and the Terms of Use, License and Disclaimer document that you must read and agree to in order to use the information, designs, and source files contained in this GitHub repository; see:

https://github.com/TeamPracticalProjects/Animatronics/blob/main/Terms_of_Use_License_and_Disclaimer.pdf (https://github.com/TeamPracticalProjects/Animatronics/blob/main/Terms_of_Use_License_and_Disclaimer.pdf)

It also contains a photo of the Head, and the master README.md file for the project.

https://github.com/TeamPracticalProjects/Animatronics/blob/main/Head.png

https://github.com/TeamPracticalProjects/Animatronics/blob/main/README.md

Data.

The Data folder contains wave (.wav) and MP3 (.mp3) format audio files that were used in the development, simulation, testing and deployment of the “Mouth” hardware and software signal processing chains. It also contains .png format photos of the simulation and test results of simulated analog circuit processing of audio files using LTSpice. The subfolder “SDCardMP3Folder” contains the MP3 format voice clip files that on the microSD card that is released with this project:

https://github.com/TeamPracticalProjects/Animatronics/tree/main/Data/SDCardMP3Folder

Documents.

The Documents folder contains the detailed documentation for this project. See the “Documentation Tree” section of this document for details.

Hardware.

The Hardware folder contains details of the hardware design for the electronic portions of this project. It contains Cadsoft Eagle electronic CAD files for the common printed circuit board that is used for both the “Brain/Eyes” PCB and the “Mouth” PCB:

https://github.com/TeamPracticalProjects/Animatronics/tree/main/Hardware/Eagle_Files

This folder also contains data sheets, manuals and other information related to the electronic components used in this project.

Legacy-NotPartOfRelease.

This folder contains some Particle Photon 1 test software that was used to determine how to operate the Mini MP3 player correctly and to couple the sampled envelope data to the mouth servo via various software processing steps. The files in this folder are NOT part of the released project but are retained for legacy research purposes.

Mechanical.

This folder contains 2D and 3D mechanical CAD files for building the structural and mechanical mounting pieces for this project. Detailed descriptions and references to these CAD files are contained in the document:

https://github.com/TeamPracticalProjects/Animatronics/blob/main/Documents/Animatronic%20H ead%20Structural-Mechanical%20Hardware%20Document.pdf (https://github.com/TeamPracticalProjects/Animatronics/blob/main/Documents/Animatronic%20Head%20Structural-Mechanical%20Hardware%20Document.pdf)

Software/Photonfirmware.

This folder contains source code files for this project, along with some legacy code that is not part of the formal release. The following subfolders contain the release software:

### https://github.com/TeamPracticalProjects/Animatronics/tree/main/Software/

Photonfirmware/AnimatronicEyesCalibration (https://github.com/TeamPracticalProjects/Animatronics/tree/main/Software/Photonfirmware/AnimatronicEyesCalibration)

Source code for the calibration software that is used to calibrate the eyes servo mechanism. See the following document for details:

https://github.com/TeamPracticalProjects/Animatronics/blob/main/Documents/Animatronic%20H ead%20Eye%20Mechanism%20Document.pdf (https://github.com/TeamPracticalProjects/Animatronics/blob/main/Documents/Animatronic%20Head%20Eye%20Mechanism%20Document.pdf)

### https://github.com/TeamPracticalProjects/Animatronics/tree/main/Software/

Photonfirmware/AnimatronicEyesTest (https://github.com/TeamPracticalProjects/Animatronics/tree/main/Software/Photonfirmware/AnimatronicEyesTest)

Source code for the “Brain/Eyes” software. See the following document for details:

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

## https://github.com/TeamPracticalProjects/Animatronics/tree/main/

Software/Photonfirmware/AnimatronicMouthDemo (https://github.com/TeamPracticalProjects/Animatronics/tree/main/Software/Photonfirmware/AnimatronicMouthDemo)

Source code for the “Mouth” software. See the following document for details:

https://github.com/TeamPracticalProjects/Animatronics/blob/main/Documents/Animatronics_Mouth_Software_Description_Document.pdf (https://github.com/TeamPracticalProjects/Animatronics/blob/main/Documents/Animatronics_Mouth_Software_Description_Document.pdf)

The remaining subdirectories are legacies of the development process and do not contain any relevant files.

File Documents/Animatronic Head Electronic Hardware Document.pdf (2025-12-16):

# Animatronics Electronic Hardware Document

By: Jim Schrempp and Bob Glicksman; v1.1, 12/15/2025


© 2025 Team Practical Projects, Bob Glicksman, and Jim Schrempp. All rights reserved.

NOTICE: Use of this document is subject to the terms of use described in the document
“Terms_of_Use_License_and_Disclai mer” that is included in this release package. This document can be found at:

https://github.com/TeamPracticalProjects/Animatronics/blob/main/Terms_of_Use_License_and_Disclaimer.pdf

© 2025, Team Practical Projects, Jim Schrempp and Bob Glicksman; all rights reserved. Subject to “Terms of Use, License and Disclosure”

TABLE OF CONTENTS.

TABLE OF CONTENTS. | 0
OVERVIEW. | 2
Custom Electronics PCB. | 3
“Brain/Eyes” Subsystem Electronics. | 6
“Brain/Eyes” PCB. | 7
Multi-Channel Servo Board. | 8
TOF Sensor. | 8
Calibration Pot and Push Button. | 8
“Mouth” Subsystem Electronics. | 8
“Mouth” PCB. | 9
Mouth Servo. | 10
Mute Backlit Push Button. | 11
Active LED. | 11
Loudspeaker. | 11
Analog Processing Theory of Operation. | 11

OVERVIEW.

This document describes the electronics used in the Animatronic Head (“Head”) project. There are two distinct electronic subsystems:

- Brain/Eyes Subsystem.
- Mouth Subsystem.

Each subsystem has its own microcontroller (Particle¹ Photon 1) and electronic connections. The two subsystems communicate with each other using Particle’s cloud-based publish and subscribe mechanism, as shown in figure 1, below.

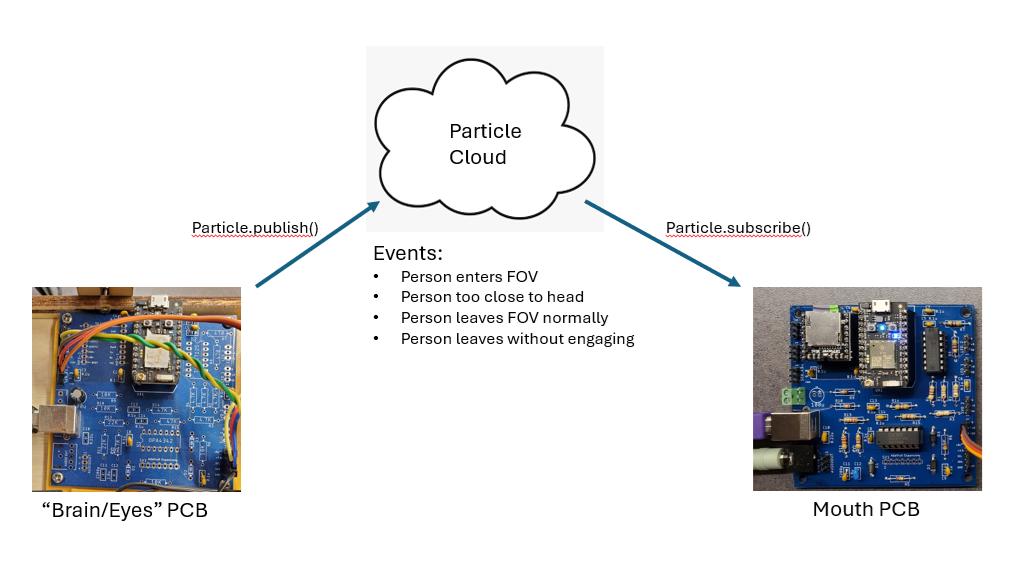
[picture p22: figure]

Figure 1. Publish and Subscribe.

The “Brain/Eyes” subsystem connects to an 8x8 time-of-flight (TOF) optical distance sensor and to a multi-servo control module. The latter controls the 6 servos of the eyes assembly. The Photon 1 microcontroller acts responsively to control the eyes position based upon real-time data from the TOF sensor.

In addition to controlling the eyes position when someone is interacting with the Head, the “Brain/Eyes” subsystem detects various significant events and publishes these to the Particle Cloud. The currently implemented events are:

1 Particle.io

- Person enters FOV: The TOF sensor data indicates that someone has entered the field of view (FOV) of the sensor and is thus in a position to interact with the Head.
- Person too close: The TOF sensor data indicates that someone has moved too close to the Head.
- Person leaves FOV normally: The TOF sensor data indicates that the sensor FOV has cleared – the engagement with the Head is over.
- Person leaves FOV quickly after arriving: The TOF sensor data indicates that the sensor FOV has cleared after only a very short time from the person arriving.

The “Mouth” subsystem responds to events published by the “Brain/Eyes” subsystem and plays an appropriate audio clip through a small loudspeaker. The Mouth subsystem electronics contains analog signal processing circuitry that processes the audio in real time to extract the “envelope” of the clip being played. This “envelope” information is further processed in Photon 1 software to drive the mouth servo in accordance with the audio being played.

A single printed circuit board has been created that is used both for the “Brain/Eyes” subsystem and for the “Mouth” subsystem. The two boards are populated differently for each of these subsystems.

CUSTOM ELECTRONICS PCB.

The schematic for the electronics printed circuit board (PCB) is shown in figure 2, below. This PCB is used both for the “Brain/Eyes” electronics and for the “Mouth” electronics. All of the electronic components are soldered to this PCB for the “Mouth” electronics board. Only a few of the parts need to be soldered to this PCB for the “Brain/Eyes” electronics board. The complete wiring for the “Brain/Eyes” and the “Mouth” electronics are covered in their individual sections of this document.

Cadsoft Eagle CAD schematic, board, and manufacturing files can be found at:

https://github.com/TeamPracticalProjects/Animatronics/tree/main/Hardware/Eagle_Files

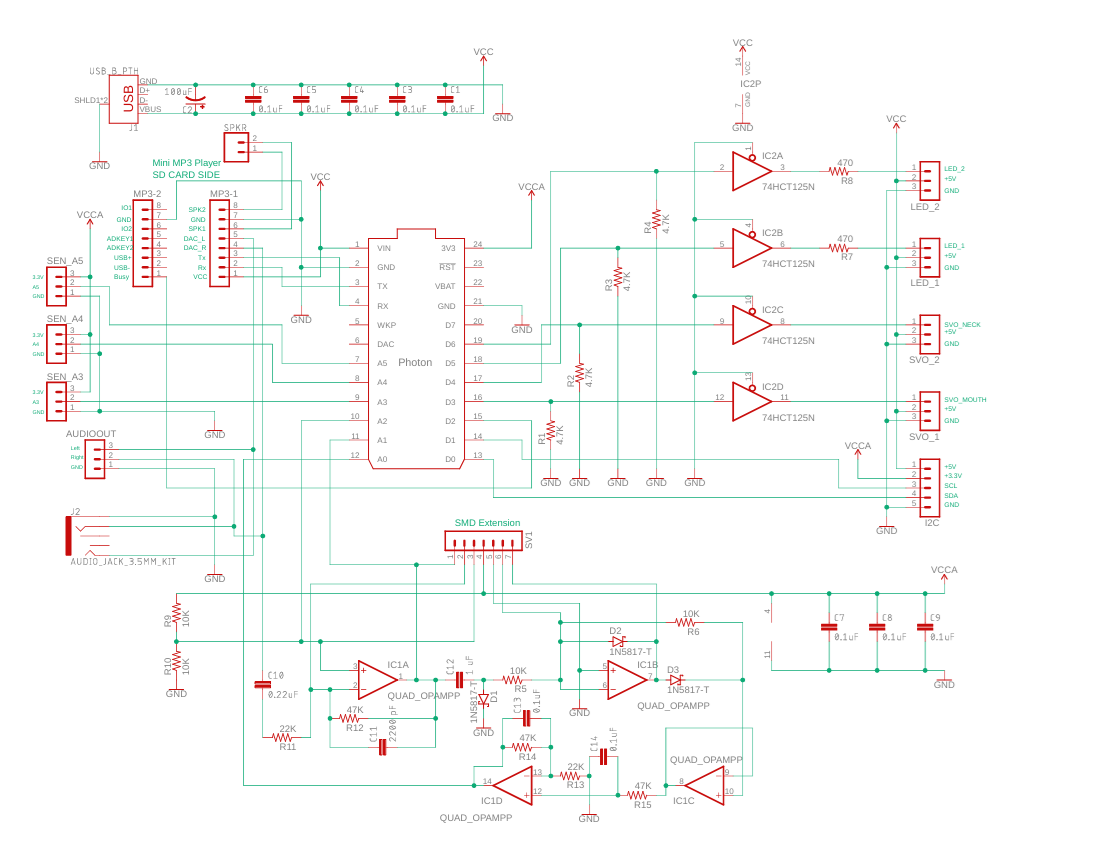
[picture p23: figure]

Figure 2. PCB Schematic

Referring the figure 2, the following are the major components on the PCB:

- Particle Photon 1. The Photon 1 is the “brains” of the electronics. The software for the Photon 1 can be found in this repository in the folder:

https://github.com/TeamPracticalProjects/Animatronics/tree/main/Software/Photonfirmw are (https://github.com/TeamPracticalProjects/Animatronics/tree/main/Software/Photonfirmware)

The individual items of software are further described in the relevant “Software” documents in the Documents folder of this repository.

Note that the Photon 1 is currently deprecated. The replacement, Particle Photon 2, is not pin compatible with the Photon 1. Particle sells an adaptor socket that allows a Photon 2 to be accommodated on a board that is designed for a Photon 1:

https://store.particle.io/products/particle-classic-adapter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 gn (https://store.particle.io/products/particle-classic-adapter)

In theory, this adapter should allow a Photon 2 to be used on this project. Some pin names may need to be redefined in the software. WARNING – we have not tested this and we cannot guarantee either the mechanical fit or the software compatibility if this adapter is used to host a Photon 2 on this project.

- Mini MP3 Player: A DFRobot DFMini MP3 Player module is used to play MP3 formatted sound clips through an external loudspeaker. Pin headers MP3-1 and MP3-2 are used to mount this module to the PCB. NOTE: Online shopping sites offer modules that are purported to be compatible with this module, but we have found that they are not. We strongly suggest using only this module:

https://www.dfrobot.com/product-1121.html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 (https://www.dfrobot.com/product-1121.html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)

The Mini MP3 Player accepts a micro SD card (up to 32 GB) that holds the MP3 files to be played.

- Quad Op-Amp (IC1) and Associated Electronic Components: An OPA4342 Quad op-amp forms the heart of the analog signal processing circuitry. This device was chosen for the following characteristics:
- It is single supply, rail to rail, low voltage capable.
- It offers FET input, very high impedance.
- It is low cost.
- It has a 1 MHz bandwidth – much more than needed for audio applications.
- It is available in DIP package format.

The last point is significant, as the PCB is designed for through-hole soldering.
However, it may be difficult to find small quantities of this part in DIP packaging. Surface mount package versions may be used with the following adapter breakout board:

https://www.adafruit.com/product/1210

In order to use this adapter on the PCB, solder a 7 pin female header to the top row of pins of IC1 and solder another 7 pin female header to the SMD Extension pin header field. You will need to solder the surface mount IC to the Adafruit adapter board and solder male pin headers to this board as well. The resulting “breakout board” can then be plugged into these female pin headers, in place of the 14 pin DIP IC.

- 74HCT125 IC (IC2): This quad, non-inverting bus driver is used as a 3.3 volt to 5 volt level shifter. Two of the outputs have current limiting resistors on the board and are intended to directly drive LEDs. The other two outputs do not have current limiting resistors and are intended to drive 5 volt servos.
- Connectors: A USB-B connector is used to supply 5 volt power to the PCB. An audio phone jack is available to connect stereo amplified speakers to the PCB, in lieu of connecting a small 8 ohm speaker directly to the PCB. The “SPKR” 2 position terminal block is used to connect a small loudspeaker (8 ohms) directly to the PCB for monaural playing of audio clips. Male pin headers are used for all other external connections to the PCB, as indicated In the relevant sections of this document, below.

“BRAIN/EYES” SUBSYSTEM ELECTRONICS.

Figure 3 is a block diagram of the “Brain/Eyes” electronics subsystem. The subsystem consists of a multi-channel servo board, a TOF sensor and the custom PCB that is configured for this application. There is also a potentiometer (Pot) and a pushbutton that are used for calibrating the 6 servo eye mechanism.


Figure 3. Brain/Eyes Electronics.

The custom PCB connects to a multi-channel servo board via the I2C bus pins on the PCB. The I2C bus is chained through the servo board and on to the TOF sensor board.

The calibration Pot is connected to the PCB using the A3 pin header field and the pushbutton is connected using the A4 pin header field.

“Brain/Eyes” PCB.

Figure 4, below, shows the assembled PCB.

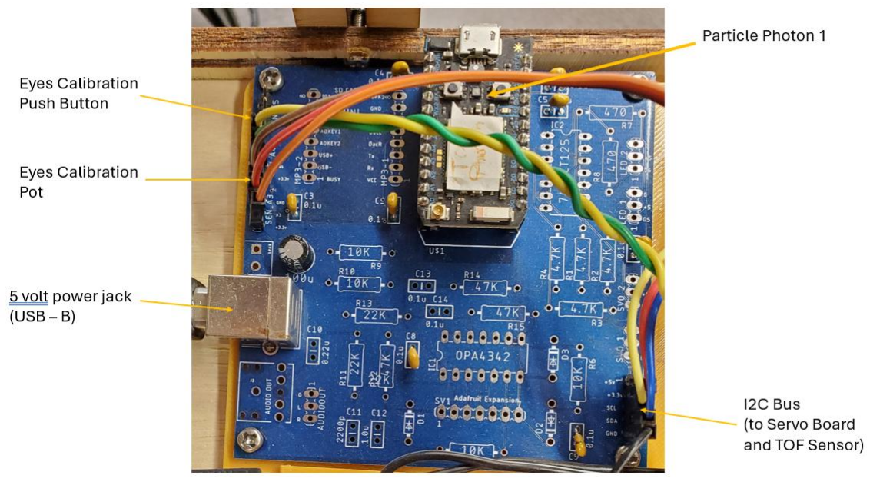
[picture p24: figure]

Figure 4. “Brain/Eyes PCB.

Only the following parts need to be loaded onto the PCB in this application:

- Particle Photon 1 (using female pin headers for mounting).
- USB-B power jack.
- Male pin headers on A3, A4, and the I2C connector fields.
- One 100uF power filtering capacitor (C2).
- Seven 0.1 uF decoupling capacitors (C1, C3, C4, C5, C6, C7, C8)

There are two sets of software that need to be flashed onto the Photon 1:

- Eyes calibration software, see: https://github.com/TeamPracticalProjects/Animatronics/tree/main/Software/Photonfirmware/AnimatronicEyesCalibration (https://github.com/TeamPracticalProjects/Animatronics/tree/main/Software/Photonfirmware/AnimatronicEyesCalibration)

- Brain/Eyes firmware, see: https://github.com/TeamPracticalProjects/Animatronics/tree/main/Software/Photonfirmware/AnimatronicEyesTest (https://github.com/TeamPracticalProjects/Animatronics/tree/main/Software/Photonfirmware/AnimatronicEyesTest)

See the “Brain Software Document” and the “Eyes Software Document” for details.

Multi-Channel Servo Board.

The Eyes mechanism uses six hobby servos. In order to drive this many servos, an Adafruit 16 channel, 12 bit PWM/servo driver board is used; see:

https://www.adafruit.com/product/815

This board has a 3.3 volt IC2 bus pass-through. It can be used to drive up to 16 servos. The first 6 servo connections are used.

TOF Sensor.

The TOF sensor is a Sparkfun Qwicc Mini ToF Imager module, see:

https://www.sparkfun.com/sparkfun-qwiic-mini-tof-imager-vl53l5cx.html

It is based on an STMicroelectronics VL53L5CX 8x8 pixel Time of Flight (TOF) image array. The module connects using 3.3 volt I2C and Qwicc connectors.

Calibration Pot and Push Button.

The six servos of the Eye mechanism need to be calibrated after the Head is assembled. Special calibration software is used for this purpose. A 10 K ohm linear potentiometer is used to manually calibrate each servo in turn. A push button switch is used to tell the calibration firmware when a pot setting is correct and should be accepted for that servo. Any momentary pushbutton can be used. We used the following part:

https://www.adafruit.com/product/1439

“MOUTH” SUBSYSTEM ELECTRONICS.

Figure 5 is a block diagram of the “Mouth” electronics subsystem. The subsystem consists of a single Servo and a small loudspeaker. There is also a green LED that lights when the mouth is active, i.e. playing a clip. A red backlit push button is provided to mute the mouth, e.g. when showing off the Head and the audio output becomes annoying. The red backlit light is lit when the mouth is muted.

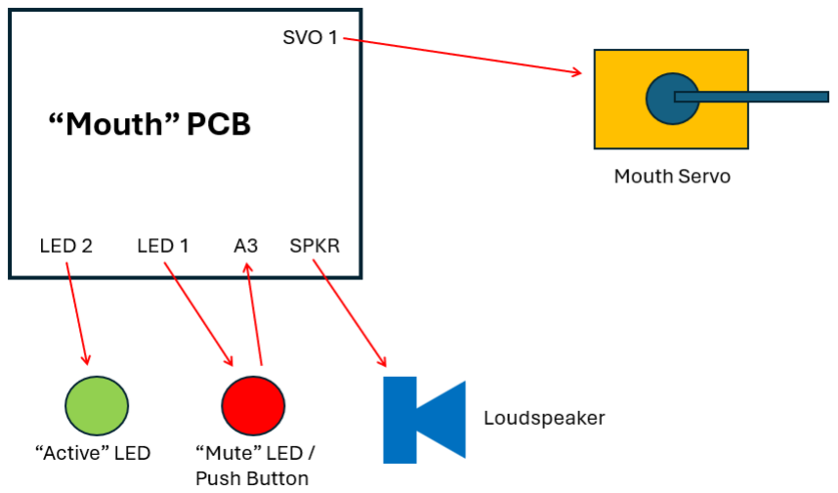
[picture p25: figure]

Figure 5. “Mouth” Electronics.

The servo is connected to the SVO-1 pin header connection field on the PCB. SVO-2 and the IC2 bus connector fields are not used in this application of the PCB.

The red push button contacts are connected to the A3 pin header connection field on the PCB and the red backlight is connected to the LED-1 pin header connection field on the PCB. The green LED is connected to the LED-2 pin header connection field on the PCB.

Pin header connection fields A4 and A5 may optionally be jumpered (to GND) to designate one of 4 “personalities” to be used by the software. A “personality” is a set of audio clips that are stored on the mini MP3 Player SD card that are to be used when interacting with the Head. You might have each personality using a different voice. Or one personality might be more sarcastic, for example.

“Mouth” PCB.

Figure 6, below, shows the assembled “Mouth” PCB. Essentially all of the parts are needed for this application.


Figure 6. “Mouth” PCB.

Figure 6 also indicates the major components on the board and what is connected to each of the pin header connection fields on the board.

Note that the mini MP3 Player can directly drive a small, 8 ohm loudspeaker. This loudspeaker is connected to the 2 position terminal strip on the PCB. Alternatively, the loudspeaker can be left off and the audio stereo phone jack used to connect amplified audio speakers to the PCB. The phone jack output is for small signals only; headphones or amplified speakers are needed.

The software that is flashed onto the Photon 1 on the “Mouth” PCB is:

https://github.com/TeamPracticalProjects/Animatronics/tree/main/Software/Photonfirmware/Ani matronicMouthDemo (https://github.com/TeamPracticalProjects/Animatronics/tree/main/Software/Photonfirmware/AnimatronicMouthDemo)

See the “Mouth Software Document” for details.

Mouth Servo.

The “Mouth” electronics can accommodate any standard 5 volt hobby servo. We chose to use a servo with metal gears and slightly more torque than the cheapest models because our mouth mechanism has a bit of weight on a lever arm that is several inches long and not counterweighted.

Mute Backlit Push Button.

We chose the following backlit red push button for the mute functionality:

https://www.adafruit.com/product/1439

Active LED.

We chose the following backlit green push button for the active indicator:

https://www.adafruit.com/product/1440

The push button is not used; only the backlit green LED is wired up.

Loudspeaker.

Any generic small 8 ohm loudspeaker may be connected to the “Mouth” PCB via the terminal strip. The 3D printed mount can accommodate a 1-1/4” diameter loudspeaker, but any 8 ohm speaker will do.

ANALOG PROCESSING THEORY OF OPERATION.

The “Mouth” PCB has analog signal processing circuitry. The purpose of this circuitry is to extract the “envelope” of the sound clip being played. The “envelope” is the amplitude modulation of the voice. The analog signal processing is basically AM demodulation.

The left channel of the headphone stereo output of the mini MP3 player is capacitively coupled into this circuitry. The amplitude of this signal is a little over 1 volt peak to peak when the mini MP3 player is playing at optimum volume.

The analog signal processing circuitry has been designed so that it may be used for other applications in the future. The circuit can be used with a microphone or other audio device by removing the mini MP3 player from its header socket and inserting a custom designed breakout board in its place. Any such alternative audio input should supply a headphone compatible audio signal with a peak-peak voltage of less than 1.5 volts.

Figure 7 is a block diagram of this circuit.


Figure 7. Analog Signal Processing Block Diagram.

The audio input from the mini MP3 player is fed through a pre-amplifier. The pre-amplifier has three functions:

- Offset the capacitively coupled audio signal by approximately +1.65 volts so that the signal is in the range of the single ended 3.3 volt power supply to this circuit.
- Provide a gain of 2 to the signal, so that the peak-peak voltage output is slightly less than 3.3 volts (for compatibility with the Photon 1 A/D converter).
- Band limit the audio signal to about 3 KHz; i.e. “telephone” signal quality.

The pre-amplifier uses one of the 4 op amps in the OPA4342 device.

The output of the pre-amplifier is fed directly into analog channel A1 of the Photon 1. The offset voltage, provided by R9 and R10, is fed directly into analog channel A2 of the Photon 1. These two analog inputs may be used by the Photon 1 software for any digital signal processing purpose. The signal is band-limited and can be sampled at 8 K samples per second (125 microseconds per sample); e.g. slightly higher than the Nyquist rate and compatible with digital audio telephone standards. NOTE: these inputs to the Photon 1 are not used in this project; they are provided for possible use on future projects.

The output of the pre-amplifier is capacitively coupled to the rest of the circuitry in order to remove the DC offset. The signal is clamped to be negative (below ground) and then fed through an inverting, idealized half wave rectifier. The resulting signal is positive (with respect to ground) and is half of the voice modulated signal.

The rectified signal is buffered and then filtered to remove the “carrier”, leaving the envelope of the signal to input to the Photon A0 analog input. A 2 pole filter with a bandwidth of approximately 40 Hz is used. The 40 Hz bandwidth was experimentally determined to contain most of the amplitude information in the signal while sufficiently removing the carrier, even for a speaker with a bass voice.


Figure 8. LTSpice Schematic for Simulation.

The analog signal processing circuit was simulated in LTSpice in order to experiment with the design and the overall design parameters. The LTSpice circuit used for the simulation is shown in figure 8. This is the same circuit that is on the PCB.

The simulation results are documented in a PowerPoint slide deck:

https://github.com/TeamPracticalProjects/Animatronics/blob/main/Documents/Analog_Processor_V2_Analysis.pptx (https://github.com/TeamPracticalProjects/Animatronics/blob/main/Documents/Analog_Processor_V2_Analysis.pptx)

The slide deck contains frequency/phase analysis of the pre-amplifier and of the envelope outputs of this circuit. The slide deck also contains time-domain (oscilloscope – like) results of feeding various types of test and simulated signals through the LTSpice simulation. The simulated inputs are .wav files produced from on-line signal generating software and also from actual voice recordings of real spoken sound clips. The .wav files themselves can be found in:

https://github.com/TeamPracticalProjects/Animatronics/tree/main/Data

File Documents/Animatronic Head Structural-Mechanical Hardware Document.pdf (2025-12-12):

# Animatronics Structural-Mechanical Hardware Document

By: Jim Schrempp and Bob Glicksman; v1.0, 12/12/2025


© 2025 Team Practical Projects, Bob Glicksman, and Jim Schrempp. All rights reserved.

NOTICE: Use of this document is subject to the terms of use described in the document
“Terms_of_Use_License_and_Disclai mer” that is included in this release package. This document can be found at:

https://github.com/TeamPracticalProjects/Animatronics/blob/main/Terms_of_Use_License_and_Disclaimer.pdf

© 2025, Team Practical Projects, Jim Schrempp and Bob Glicksman; all rights reserved. Subject to “Terms of Use, License and Disclosure”

TABLE OF CONTENTS.

TABLE OF CONTENTS. | 1
DOCUMENT OVERVIEW. | 2
STRUCTURAL FRAME. | 3
EYES MECHANICAL AND ELECTRONIC MOUNTING. | 5
MOUTH ELECTRONIC AND MECHANICAL MOUNTING. | 7
SPEAKER MOUNTING. | 9
FACE COMPONENTS. | 10

DOCUMENT OVERVIEW.

This document describes the structural and mechanical components of the Animatronic Head project. This project was designed for experimentation more than for any specific use. Therefore, a very flexible structural framework was developed. Figure 1 depicts this structure:


Figure 1. Structural Overview.

The main part of the structural assembly is the frame. The frame provides overall mechanical support for the electronic components, mechanical components, and the face. The frame contains moveable platforms onto which electronic and mechanical components are mounted. The frame also provides mounting for 3D printed magnet holders. Magnets are glued to these holders and are used to hold 3D printed face components onto the frame at adjustable positions.

2D and 3D mechanical CAD files for all of these structural and mechanical components are in the Mechanical folder in this Repository:

https://github.com/TeamPracticalProjects/Animatronics/tree/main/Mechanical

STRUCTURAL FRAME.

Figure 2 shows a side view photo of the Animatronic Head. This photo shows how the various electronic and mechanical components of the Head are mounted on, and supported by, the frame.


Figure 2. Structural Frame Photo.

The frame assembly has two movable shelves and a non-movable base. The top shelf holds the eyes mechanism and the eyes electronics. The middle shelf holds the mouth mechanism and the mouth electronics. The base (bottom shelf) holds the loudspeaker.

The shelf positions are adjustable using wingnuts. This adjustability allows each shelf to be positioned so that the mechanical components align with the openings in the face.

The face itself is in three pieces:

- Crown: the top of the head. Cosmetic only.
- Eyes: mounts the TOF sensor and has holes for the eyes mechanical assembly.
- Mouth: has a cutout for the movable jaw mechanism.

The three face components are held onto the frame using magnets. See the section on the face, below, for details.

Figure 3 is a 3D rendering of the frame.


Figure 3. Structural Frame 3D Rendering.

The frame components are laser cut from 6mm birch plywood. The frame, shelves and base pieces are glued together. The shelves are mounted using screws with wingnuts through the slots in the vertical rails so that they may be adjusted properly to fit behind the face.

CAD files for the frame are in the Mechanical folder in this Repository; see:

https://github.com/TeamPracticalProjects/Animatronics/tree/main/Mechanical/armature

# EYES MECHANICAL AND ELECTRONIC

MOUNTING.

The eyes mechanism and the eyes electronics are mounted on the top shelf of the frame, see figure 4.


Figure 4. Eyes Mechanism and Electronics Mounting.

The eyes mechanism is attached to the shelf using double sided tape. It can be placed precisely to align with eye holes in the face. The electronics consists of a custom printed circuit board and a commercial 16 channel servo control board; for details, see:

https://github.com/TeamPracticalProjects/Animatronics/blob/main/Documents/Animatronic%20H ead%20Electronic%20Hardware%20Document.pdf (https://github.com/TeamPracticalProjects/Animatronics/blob/main/Documents/Animatronic%20Head%20Electronic%20Hardware%20Document.pdf)

A 3D printed mounting plate is used to secure both of these electronic circuit boards. The assembled 3D printed mounting plate is attached to the shelf using double sided tape. The CAD file for this mounting plate is:

https://github.com/TeamPracticalProjects/Animatronics/blob/main/Mechanical/PCBMount/eye%20base%20plate.3mf (https://github.com/TeamPracticalProjects/Animatronics/blob/main/Mechanical/PCBMount/eye%20base%20plate.3mf)

A potentiometer and a momentary push button switch are used to calibrate the eyes mechanism after assembly. A 3D printed mounting bracket holds these components and is attached to the shelf using double sided tape. Figure 5 is a detailed view of this assembly.


Figure 5. Eyes Calibration Controls Mounting Detail.

The 16 channel servo board has its own 5 volt power source via a USB power connector (see figure 4, above). A 3D printed mounting plate holds this connector and is attached to the shelf using double sided tape.

3D CAD files for these mounting brackets are in:

https://github.com/TeamPracticalProjects/Animatronics/blob/main/Mechanical/PCBMount/eye%20control%20mount.f3d (https://github.com/TeamPracticalProjects/Animatronics/blob/main/Mechanical/PCBMount/eye%20control%20mount.f3d)

The eyes mechanism itself is an intricate assembly consisting of six hobby servos and an integrated set of 3D printed parts. We adapted the following excellent mechanism from Will Cogly’s design on the Internet; see:

https://www.instructables.com/Simplified-3D-Printed-Animatronic-Dual-Eye-Mechani/

The maker, Will Cogley, is incredibly inventive. His YouTube channel has a lot of amazing things:

https://www.youtube.com/channel/UCkUD_8b1JoTL2ipOVtxfNKw

We modified a few of the eye mechanism parts, see:

https://github.com/TeamPracticalProjects/Animatronics/tree/main/Mechanical/EyeMech

# MOUTH ELECTRONIC AND MECHANICAL

MOUNTING.

The mouth mechanism and the mouth electronics are mounted on the middle shelf of the frame, see figures 6, 7 and 8. Figure 6 shows the mouth control electronics. Details of the electronic design are in the document:

https://github.com/TeamPracticalProjects/Animatronics/blob/main/Documents/Animatronic%20H ead%20Electronic%20Hardware%20Document.pdf (https://github.com/TeamPracticalProjects/Animatronics/blob/main/Documents/Animatronic%20Head%20Electronic%20Hardware%20Document.pdf)


Figure 6. Mouth Electronics Mechanical Assembly.

The electronic printed circuit board is affixed to a 3D printed mounting plate – the same mounting plate design that is used to mount the eyes electronics:

https://github.com/TeamPracticalProjects/Animatronics/blob/main/Mechanical/PCBMount/eye%20base%20plate.3mf (https://github.com/TeamPracticalProjects/Animatronics/blob/main/Mechanical/PCBMount/eye%20base%20plate.3mf)

The electronics assembly is attached to the shelf using double sided tape.

Two, backlit, pushbutton switches are used to indicate when the mouth is speaking and to allow the demonstrator to mute the loudspeaker. These components are mounted on a 3D printed bracket that is affixed to the shelf using double sided tape; see figure 7. A 3D CAD file for this bracket is found in:

https://github.com/TeamPracticalProjects/Animatronics/blob/main/Mechanical/PCBMount/mouth %20switch%20mount.3mf (https://github.com/TeamPracticalProjects/Animatronics/blob/main/Mechanical/PCBMount/mouth%20switch%20mount.3mf)


Figure 7. Mouth Mute Controls.

The mouth mechanism itself is shown in figure 8, below. It is mounted on the same middle shelf as the mouth electronics, see figure 8.


Figure 8. Mouth Mechanical Assembly.

The mouth is driven by a servo that connects to the jaw of the face with a 3D printed adjustable assembly. CAD files for these 3D printed parts are in:

https://github.com/TeamPracticalProjects/Animatronics/tree/main/Mechanical/MouthMech

The jaw itself is 3D printed; see:

https://github.com/TeamPracticalProjects/Animatronics/blob/main/Mechanical/Head/mouth.3mf

SPEAKER MOUNTING.

A small loudspeaker is used to play back audio clips. It is mounted on the base of the frame using a 3D printed bracket; see figure 9.


Figure 9. Loudspeaker Mounting.

3D CAD file for this bracket is in:

***** CAD FILE IS MISSING !!!! *****

This bracket is mounted to the base using double sided tape.

FACE COMPONENTS.

The face consists of four 3D printed components, see figure 10:


Figure 10. Face.

The CAD files for these components are:

- The Crown. See:

***** CAD FILE IS MISSING !!!! *****

- The Eyes. See:

https://github.com/TeamPracticalProjects/Animatronics/blob/main/Mechanical/Head/Eye s%20Front.3mf (https://github.com/TeamPracticalProjects/Animatronics/blob/main/Mechanical/Head/Eyes%20Front.3mf)

- The Mouth. See:

https://github.com/TeamPracticalProjects/Animatronics/blob/main/Mechanical/Head/Mou th%20Front.3mf (https://github.com/TeamPracticalProjects/Animatronics/blob/main/Mechanical/Head/Mouth%20Front.3mf)

- The Jaw. See:

https://github.com/TeamPracticalProjects/Animatronics/blob/main/Mechanical/Head/mou th.3mf (https://github.com/TeamPracticalProjects/Animatronics/blob/main/Mechanical/Head/mouth.3mf)

These 3D printed components are attached to the frame using magnets. 3D printed “ears” are attached to the frame using screws and wingnuts; see figure 110, below.


Figure 11. Face Mounting Magnet Ears.

Magnets are glued to these ears in the proper position to hold the face components to the frame. These magnetic “ears” provide fine adjustment of the face components on the frame to precisely align with the shelves on which the mechanical eyes and mouth assemblies are located. 3D CAD files for these mounting ‘ears” are in:

https://github.com/TeamPracticalProjects/Animatronics/tree/main/Mechanical/Head

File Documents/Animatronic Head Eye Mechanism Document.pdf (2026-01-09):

# Animatronics Eye Mechanism Document

By: Jim Schrempp and Bob Glicksman; v1.2, 1/08/2026


© 2026 Team Practical Projects, Bob Glicksman, and Jim Schrempp. All rights reserved.

NOTICE: Use of this document is subject to the terms of use described in the document
“Terms_of_Use_License_and_Disclai mer” that is included in this release package. This document can be found at:

https://github.com/TeamPracticalProjects/Animatronics/blob/main/Terms_of_Use_License_and_Disclaimer.pdf

© 2026, Team Practical Projects, Jim Schrempp and Bob Glicksman; all rights reserved. Subject to “Terms of Use, License and Disclosure”

TABLE OF CONTENTS.

TABLE OF CONTENTS. | 1
DOCUMENT OVERVIEW | 2
Eyes mechanism | 2
Basic Eyes Movements | 2
Eye calibration | 2

# DOCUMENT OVERVIEW

This document provides a high level description of the eye component of the animatronic head.

## EYES MECHANISM

The eyes mechanism is taken directly from the popular and talented Will Cogley who works as Niehelm Megatronics. Will has:

- A Patreon page: https://www.patreon.com/c/Will_Cogley/posts
- A YouTube channel: https://www.youtube.com/@WillCogley

Your best place to start is this Instructable of the eye mechanism we used. https://www.instructables.com/Simplified-3D-Printed-Animatronic-Dual-Eye-Mechani/ It gives step-by-step instructions for making the eyes.

Note that in the years since we chose this mechanism, Will has released newer versions that are even more clever in their assembly. All of his mechanisms should work with our software.

The original mechanism was a bit too big to fit closely into the animatronic head. As a result, we modified the base of the mechanism slightly. You can find our modified STL files in this repository.

## BASIC EYES MOVEMENTS

The eyes have five different motions.

1. Up and Down. The eyes are coupled and move together.
2. Left and Right. Also coupled together and move at the same time.
3. Four eyelids, one upper and one lower on each eye. The eyelids move independently.

## EYE CALIBRATION

Every servo can react slightly differently to the same positioning command. In addition, the linkage from the servo to the mechanism can be mounted on the servo horn at a slightly different angle. For these reasons, calibration is required.

The repository contains a calibration program in the folder: Software / Photonfirmware / AnimatronicEyesCalibration When loaded into the Particle Photon 1 it will move the eyes and eyelids to what it expects to be the two extents of movement. For example, it will move the eyes fully up and then fully down. Each time it will print out the servo command value it is using to the serial port.

Your job is to adjust the mechanism, the mounting of the linkage to the servo horn, or the values being used by the calibration firmware. You want to find values that will command each servo to push the mechanism to its extent, but not beyond. You don’t want the servos to stall.

The calibration software uses a potentiometer and a push button switch. The potentiometer is used to manually move the selected servo to the correct position, as indicated by prompts on the serial monitor. The pushbutton is used to enter that servo calibration value and move on to prompting the user for the next servo calibration value.

The calibration program will print out a series of steps to follow. For instance, it might say, “Opening the left upper eyebrow”. Your job is to slowly turn the potentiometer until the left upper eyebrow is fully open. Then press the button to move on to the next calibration step.

After you have a completed calibration, the calibration program will print out a code block of constants that you can copy and paste into the actual animatronic code. The code block goes in the file eyeservosettings.h

If you have several mechanisms, you may want to alter the animatronic code to use #defines to indicate which of your mechanisms you are compiling for. In our experience each mechanism will be significantly different.

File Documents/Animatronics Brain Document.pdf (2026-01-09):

# Animatronics Brain Document

By: Jim Schrempp and Bob Glicksman; v1.2, 1/08/2026


© 2026 Team Practical Projects, Bob Glicksman, and Jim Schrempp. All rights reserved.

NOTICE: Use of this document is subject to the terms of use described in the document
“Terms_of_Use_License_and_Disclai mer” that is included in this release package. This document can be found at:

https://github.com/TeamPracticalProjects/Animatronics/blob/main/Terms_of_Use_License_and_Disclaimer.pdf

© 2026, Team Practical Projects, Jim Schrempp and Bob Glicksman; all rights reserved. Subject to “Terms of Use, License and Disclosure”

TABLE OF CONTENTS.

TABLE OF CONTENTS. | 0
DOCUMENT OVERVIEW. | 2
Theory of Operation | 2
Software Layout | 2
Software Layers | 3
The software stack | 4
Time of Flight sensor (the real “eyes”) | 5
Noise Rejection | 5
Eye Tracking | 6

DOCUMENT OVERVIEW.

- Theory of Operation
- How the software is structured
- 8x8 TOF Sensor
- Room Calibration
- Noise rejection
- Spatial processing
- Temporal processing
- Events
- Scenes and Scenarios
- Eye tracking based upon sensor data

## THEORY OF OPERATION

## Software Layout

The software to run the puppet is in:

https://github.com/TeamPracticalProjects/Animatronics/tree/main/Software/Photonfirmware/Ani matronicEyesTest (https://github.com/TeamPracticalProjects/Animatronics/tree/main/Software/Photonfirmware/AnimatronicEyesTest)

The main “brain” software is in AnimatronicEyes.ino and this is the place to start your learning. Other notable files in the src folder are:

- TPP_Animatronic_Global.h - Of interest is the TOF_Detect enumeration. This is a list of ways the puppet may interpret data from the ToF sensor, which then drives behavior.
- TPPAnimateServo - The class object TPP_AnimateServo that controls a servo. One instance per servo.
- TPPAnimatePuppet - The class object TPP_Puppet that controls coordination between servos to give a life-like look to the puppet’s actions. This class would make sure that when the left upper eyelid closes, the lower left one closes too. One instance and it owns all the AnimateServo objects.
- TPPAnimationList - This class animationList is used to chain a series of “scenes” together over time. For instance, “GoToSleep” might have both eyes slowly close, then one eye open just a bit before it finally closes too.
- AnimatronicEyes.ino - The main program and the “brain” of the puppet. This code takes input from sensors (just the ToF sensor at this point), decides the emotional state of the puppet (bored, alert, asleep, etc), decides what - if any - actions to take based on the current emotional state and the current sensor input. This code owns the AnimationList and AnimatePuppet objects.

- eyeservosettings.h - Holds the constants for the particular eye mechanism discovered when you run the eye calibration software.

## Software Layers

Starting at the lowest layer, each servo is controlled by an instance of the TPP_AnimateServo class. You call this class with a command to move to a certain position at a certain speed and the class object will make it happen in a non-blocking way.

The next layer up is one instance of the class TPP_Puppet. This class owns all the TPP_AnimateServo objects. It can handle coordinated movements. For example, we have a method to “blink”. This requires the coordinated movement of four servos, one for each eyelid. In this method we might also have the focus of the eyes move just a bit to make the overall operation more life-like. If we had a servo to move the entire head left-right, then this would be the object to implement moving the eyes at the same time the head moves so that the eyes remain focused on one spot in space.

On top of TPP_Puppet we have animationList. A scene is a group of TPP_Puppet method calls. An animationList is a set of Scenes that happen over time. For example, one scene might be: Look Up and Left and blink. A second scene might be: Look right, close the eyes slowly, then quickly open the right eye only. The animationList object can be used to make these two scenes play out over time:

1. Starting immediately, move from the current positions to scene 1.
2. Starting in 10 seconds, move from the now current positions to scene 2.

By stringing together a series of well thought out scenes, complex animation sequences can be run to make the head appear life-like.

animationList provide the ability to have higher level concepts such as “go to sleep” or “wake up and look at the closest object” or (if we had neck movement) “wake up, quickly look at the nearest object and then slowly rotate the head so that it is facing the object head on”.

main() | Calls animationList.process()

Class: animationList | A singleton. Define a series of “scenes” (mechanism positions) and then run through them as the clock ticks. ● addScene(scene, speed, delay) - predefined, or mechanism by mechanism ● startAnimation() ● stopAnimation() ● clearSceneList()
Class: TPP_Puppet | One for each puppet (we have only one); owns animateServo objects ● eyeball.look(x, y, speed) ● eyelid.open(position, speed) ● mouth.open(position, speed) ● Puppet ○ eyesOpen() ○ blink() ○ wink()
Class: TPP_AnimateServo | An instance for each servo. Moves servo slowly, or quickly. ● moveTo(x, speed)

## The software stack

How it works.

1. AnimatronicEyes.ino
a. Call TPP_TOF.getPOI or TPP_TOF.getPOITemporalFiltered(pointOfInterest *pPOI);
i. Returns the current Point of Interest as determined by the TPP_TOF object. If the Temporal Filtered version is called, then it only reports a POI if the POI has persisted for a few seconds. This slows the puppet’s response to new stimuli, but avoids reacting to spurious detections in the field of view.
ii. | Decide if this is a new POI and if so then how should the puppet react
iii. | Call for an animationList or directly command the TPP_Puppet
b. Mainloop calls animationList.process()
c. Of particular interest is processEventsStateMachine and the enum headStates. This is where the “brain” decides what action to take based on new sensor data and the current emotional state of the puppet.
2. animationList.process()
a. notes elapsed time and decides if there is a new scene to set.
b. Calls TPP_Puppet to set new scene positions.
c. Calls TPP_Puppet.process()

3. TPP_Puppet.process()
a. Decides if the movement of one servo affects another (e.g. moving eyes all the way left might cause the head to rotate left)
b. Calls TPP_AnimateServo.process() for each servo it owns
4. TPP_AnimateServo.process()
a. Notes current servo position vs target servo position
b. Notes time and moves servo towards target position, if needed

## TIME OF FLIGHT SENSOR (THE REAL “EYES”)

The head uses an 8x8 optical Time of Flight sensor to detect objects in front of it. The ToF sensor provides an 8x8 matrix of values. Each value is the distance, in millimeters, to the closest object in that area of the field of view. If the closest object is more than about 8 feet away, then the sensor detects nothing.

When the puppet starts up it reads the current value of the ToF matrix and assumes that the distances it detects are all static objects in the environment. When the head first boots it is important that it is looking at a stable “no activity” field of view. After this the ToF sensor runs a new matrix 14 times a second. If our code is fast enough, it will consider each of the frames; if not we might miss one or two but that does not affect the operation of the “brain”. On each read the brain assumes that deviations from the static background are objects it should be aware of. It is important that the head and background objects remain fixed or else the head will think objects have entered its field of view.

(We have plans, not implemented, to periodically re-sense the background objects. Our idea is that when the ToF values have not changed for 3 seconds, then the current ToF matrix should become the new background. The ToF is very sensitive, so a person standing still in front of it will always be seen to move slightly.)

For example, if nothing has changed from the start-up reading, the brain might decide that it is bored and put the eyes to sleep. Or it might decide to speak something like “Is any one out there?” while the eyes flit around a bit.

As another example, if the ToF data shows that something has entered the field of view the brain might decide to have the eyes “look” in that direction and the mouth to say, “hi there!”

The ToF sensor might detect several objects in the field of view. The brain has to sort these out and decide which ones to consider important. It favors ones that are closer and bigger over ones that are further away and smaller.

## Noise Rejection

The ToF sensor is sensitive to even millimeter changes in distance. It is also subject to false readings due to multi-path distortion. For these reasons we have to do some filtering of the raw data.

Temporal filtering is done to make sure a new object is truly a new object and not just noise. The brain keeps several readings of the ToF sensor matrix. If a new object is only seen for a fleeting time, then we assume it was just noise from the ToF. Today a new object must be seen in two subsequent detection calls to be considered a Point of Interest.

Spatial filtering is done to determine which object is nearest. The brain considers adjoining cells in the 8x8 matrix. We average the ToF distance of adjacent cells to get the distance we will consider for a cell. We then consider the distance to each cell and direct the eyes to the cell with the nearest detection.

## EYE TRACKING

When the brain detects an object in its field of view it might decide to look at it. This means that the eyes must open and the eyes move vertically and horizontally to “look” at the object. As the object moves in the field of view of the TOF sensor, the brain may want to keep the eyes pointed at the object so that the eyes appear to track the object as it moves.

To make the movement appear more natural, the brain might have the eyes begin to move quickly towards the target, then slow as they approach their target position. Once in position, the eyes might have small saccade movements to improve the life-like feeling of the whole head. The eyes might blink from time to time. Blinking and saccade should be controlled below the "conscious" part of the brain, being a function of the eye class itself. The higher level "conscious" brain class should be able to instruct the eyes to “stare” and the eyes should not blink for a while, but eventually the eyes will need to blink.

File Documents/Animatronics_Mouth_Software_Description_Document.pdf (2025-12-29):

# Animatronics Mouth Software Description Document

By: Jim Schrempp and Bob Glicksman; v1.1, 12/29/2025


© 2025 Team Practical Projects, Bob Glicksman, and Jim Schrempp. All rights reserved.

NOTICE: Use of this document is subject to the terms of use described in the document
“Terms_of_Use_License_and_Disclai mer” that is included in this release package. This document can be found at:

https://github.com/TeamPracticalProjects/Animatronics/blob/main/Terms_of_Use_License_and_Disclaimer.pdf

© 2025, Team Practical Projects, Jim Schrempp and Bob Glicksman; all rights reserved. Subject to “Terms of Use, License and Disclosure”

TABLE OF CONTENTS.

TABLE OF CONTENTS. | 1
Document Overview. | 2
“Mouth” Software Overview. | 2
“Mouth” Software Files. | 3
“Mouth” Software Settings and Calibration. | 3
Personality Setting and Definition. | 3
Mouth Mechanism Calibration. | 4
Clip Processing Value Determination and Setting. | 6
Clip Testing. | 9
Tips on Recording Audio Clips. | 11
Clip Volume. | 11
Enunciation. | 11

DOCUMENT OVERVIEW.

This document describes the software (firmware) that runs the Animatronic Head “Mouth” subsystem. This subsystem is described in the document:

https://github.com/TeamPracticalProjects/Animatronics/blob/main/Documents/Animatronic%20H ead%20Electronic%20Hardware%20Document.pdf (https://github.com/TeamPracticalProjects/Animatronics/blob/main/Documents/Animatronic%20Head%20Electronic%20Hardware%20Document.pdf)

“MOUTH” SOFTWARE OVERVIEW.

The “Mouth” software runs on a Particle¹ Photon 1 using Particle OS version 3.0.0²

The “Mouth” software subscribes to events that are published to the Particle Cloud by the Animatronic “Brain/Eyes” software. Each event causes an audio clip to be selected and played through the DFRobot DFPlayer miniMP3 module and its associated micro SD card. While a clip is being played, the “Mouth” software samples the envelope of the audio clip (every 10 milliseconds, from pin A0) and processes each sample using a digital signal processing chain that includes:

- Number of samples to average (for smoothing); typically set to 1 (no smoothing)
- Optional non-linear scaling of the sample values; typically set to linear.
- Scaling of A/D values based upon maximum and minimum clip amplitude values and mapping to the range of the mouth servo.

The best overall effect for any specific audio clip is determined experimentally using Particle Cloud functions and variables that can be read and set using the Particle Console. The values for each clip on the micro SD card are stored in a separate file in the software. The software uses the values in this file to process each A/D sample into Mouth servo position values.

A backlit push button is provided to mute the mouth temporarily, e.g. when presenting the Head in a demo.

The “Mouth” software supports up to 4 “personalities”. Each personality represents a set of audio clips; e.g. different personalities can have different voices and messages for each event published by the “Brain/Eyes” software. Up to 4 audio clips can be associated with each event

1 Particle.io
2 This is the latest version of the Particle OS that compiles on a Photon 1 and does not generate errors when compiling the DFRobot DFMini MP3 Player library. This library has several bugs in it. All bugs relate to lack of a return statement in functions that have non-void return values. None of these functions are used by this code. OS 3.0.0 treats these issues as warnings and compiles OK. Later versions of the Particle OS treat them as fatal errors and will not compile the code even though the offending functions are not used.

in each of the 4 personalities. When the “Mouth” software responds to an event, one of the clips associated with that personality and that event is randomly selected and played.

A set of defined constants in the software determines the maximum open and closed positions for the mouth servo. The open and closed positions that give the best visual effect is determined experimentally, as it varies with the face hardware architecture and mouth servo mechanics. Mouth open and closed values can be experimented with using Cloud functions that are available through the Particle Console.

“MOUTH” SOFTWARE FILES.

The source code files for the “Mouth” software are located in this repository, at:

https://github.com/TeamPracticalProjects/Animatronics/tree/main/Software/Photonfirmware/Ani matronicMouthDemo (https://github.com/TeamPracticalProjects/Animatronics/tree/main/Software/Photonfirmware/AnimatronicMouthDemo)

The following files are located in this folder:

- lib/DFRobotDFPlayerMini. This is the library for the DFRobot DFPlayer miniMP3 device.
- src/MN_Demo_Mouth.ino. This is the main code for the “Mouth” software.
- src/TPP_Animatronic_Global.h. This file defines enumerated event codes for the events that are published by the “Brain/Eyes” software and subscribed to by the “Mouth” software.
- src/TPP_clipinfo.h. This file defines the standard C structure (struct) that must be available for each clip that is to be played and processed.
- src/TPP_clipinfo.cpp. This file contains the actual values of the standard clip struct for each MP3 clip file that is used by the Head. The values contained in these structs are determined experimentally (using the Particle Console) to provide the best audio volume and best visual mouth movement effect when playing each audio clip.

“MOUTH” SOFTWARE SETTINGS AND CALIBRATION.

Personality Setting and Definition.

Jumper fields A5 and A4 may be used to select one of 4 “personalities” for the “Mouth” software to use. Each personality is a set of audio clips stored on the micro SD card, with up to 4 clips for each possible event that the “Mouth” software subscribes to. An open pin is a logic 1 and a grounded pin is a logic 0. The “Mouth” software reads these pins during setup() and sets the personality.

A default set of clips and personalities is included in this repository. The personalities are:

Bob Personality #1: ground both A4 and A5
Bob Personality #2 (not yet implemented): ground A5, open A4
Jim Personality #1: open A5, ground A4
Jim Personality #2 (not yet implemented): open A5, open A4

The details of each of these “personalities” are defined in:

https://github.com/TeamPracticalProjects/Animatronics/blob/main/Software/Photonfirmware/AnimatronicMouthDemo/src/TPP_clipinfo.cpp (https://github.com/TeamPracticalProjects/Animatronics/blob/main/Software/Photonfirmware/AnimatronicMouthDemo/src/TPP_clipinfo.cpp)

The clips themselves are contained in:

https://github.com/TeamPracticalProjects/Animatronics/tree/main/Data/SDCardMP3Folder

Mouth Mechanism Calibration.

The Mouth mechanism is a single servo that attaches the jaw piece of the Head via a lever arm. The servo positions for the Mouth closed and Mouth wide open are dependent on the mechanical details of this mechanism and on the initial servo position during Head assembly. The Mouth closed servo position (angle) should be set so that the Mouth is almost touching the upper lip (leaving a little room for mechanical bounce). The Mouth open position should be set for the best visual effect – open enough to make all movement easily visible but not open so much that the effect is unrealistic.

The settings for any newly constructed Head must be determined experimentally using the Particle Console. See figure 1 for details:


Figure 1. Mouth Position Calibration Control.

The argument for the “Mouth Position” Cloud function, shown in figure 1, is the servo angle. Entering a number in the Argument field and clicking on Call will cause the Mouth servo to go to that position. The best values for open and closed servo positions should be noted and then entered into the “Mouth” software:

https://github.com/TeamPracticalProjects/Animatronics/blob/main/Software/Photonfirmware/AnimatronicMouthDemo/src/MN_Demo_Mouth.ino (https://github.com/TeamPracticalProjects/Animatronics/blob/main/Software/Photonfirmware/AnimatronicMouthDemo/src/MN_Demo_Mouth.ino)

See lines 94 and 95 for these defined constants.

Note that the servo angle change between open and closed of the default values is only about 11 degrees. A larger difference in servo angle makes the open Mouth position too wide and unrealistic in appearance.

The “Mouth” software must be recompiled and flashed to the Mouth Photon 1 after this file is changed.

Clip Processing Value Determination and Setting.

The digital signal processing settings for each clip that is to be played on the Head should be calibrated for the best overall visual effect. The clip calibration data for each clip is defined by a C structure. The definition of this C structure is in:

https://github.com/TeamPracticalProjects/Animatronics/blob/main/Software/Photonfirmware/AnimatronicMouthDemo/src/TPP_clipinfo.h (https://github.com/TeamPracticalProjects/Animatronics/blob/main/Software/Photonfirmware/AnimatronicMouthDemo/src/TPP_clipinfo.h)

The actual data for each clip is added to the relevant “personality” in the file:

https://github.com/TeamPracticalProjects/Animatronics/blob/main/Software/Photonfirmware/AnimatronicMouthDemo/src/TPP_clipinfo.cpp (https://github.com/TeamPracticalProjects/Animatronics/blob/main/Software/Photonfirmware/AnimatronicMouthDemo/src/TPP_clipinfo.cpp)

The “Mouth” software must be recompiled and flashed to the Mouth Photon 1 after these files are changed.

The best values to use for any given clip will depend upon the clip playback volume and the actual contents of the audio clip. The best overall effect for each clip is determined experimentally using Particle Cloud functions and variables available through the Particle Console; see figure 2, below.


Figure 2. Clip Settings for Clip Calibration Testing.

The “clip number” function Argument is the number preceding the clip file’s name, e.g. a clip file named “0110 HelloThere.mp3” can be played by entering “0110” in the “clip number” Argument and clicking on Call.

Prior to playing a clip, some reasonable defaults should be set into each of the following functions:

- volume: use a number like 23 (max is 30).
- number of samples: use 1 (no sample averaging)
- non-linear processing type: use 1 (linear processing; either 1 or 2)
- analog input max: use 4095 (max is 4095)
- analog input min: use 0 (min is 0)

The Argument for each function must be set by clicking on the relevant Call button. Once the Arguments are set in the software, the functions do not have to be called again for subsequent experiments, unless you want to try changing them.

Note that the playback “volume” setting is most important as it affects the volume of the sound through the loudspeaker as well as the amplitude of the analog signal into the Photon 1 A/D converter. The loudness of the playback sound will depend upon the parameters used when originally recording the clip. See below for tips on proper clip recording.

The “volume” function Argument should be set to play the clip using the best audio volume. The default settings for “analog input max” and “analog input min” should be set to the overall max and min of the Photon 1 A/D converter (4095 and 0, respectively). The “clip number” function should then be called to play the clip and assess the sound playback volume. The “volume” function should then be changed in order to achieve the best playback volume. When the best playback volume is achieved, click on “max envelope value” and “min envelope value” (see figure 3) in order to determine the highest and lowest A/D converter values during the last clip playback.

In general, the “min envelope value” should be 0 (or very close to 0). If so, set the “analog input min” to be zero. If this value is not close to 0, then the analog circuitry is noisy – this is a hardware problem that should be corrected.

In general, the “max envelope value” will be somewhere between about 2500 and 4000. This will vary with the clip and the volume setting that is selected. It is important to scale the “analog input max” to be close to 4095 (the A/D converter max) but with a little headroom. This way, the scaling process will move the mouth for the best effect. The value to set for “analog input max” should be slightly higher than the “max envelope value” for this reason. Change “analog input max” and replay the clip to see that the “max envelope value” is now around 4000 (not critical but must be less than 4095).

You may experiment with changing the other parameters to observe the best Mouth effect for that clip. In general, averaging samples or selecting non-linear processing does not make a large visual difference, but improvement over the defaults may be possible. The final effect is, of course, subjective.

Once all of these values are experimentally optimized. The clip information (the arguments to these Cloud functions that produce the best visual effect) should be entered/edited in the file:

https://github.com/TeamPracticalProjects/Animatronics/blob/main/Software/Photonfirmware/AnimatronicMouthDemo/src/TPP_clipinfo.cpp (https://github.com/TeamPracticalProjects/Animatronics/blob/main/Software/Photonfirmware/AnimatronicMouthDemo/src/TPP_clipinfo.cpp)

The “Mouth” software must then be re-compiled and flashed to the Mouth Photon 1.


Figure 3. Max/Min A/D Values for a Clip.

Clip Testing.

The overall process of triggering the “Mouth” software from a Particle event and playing the clip with appropriate Mouth movement can be tested using the Particle Console; see figure 4, below.


Figure 4. Testing an Event.

The Argument to the “mouth_event” function is the event number. Event definitions are in the file:

https://github.com/TeamPracticalProjects/Animatronics/blob/main/Software/Photonfirmware/AnimatronicMouthDemo/src/TPP_Animatronic_Global.h (https://github.com/TeamPracticalProjects/Animatronics/blob/main/Software/Photonfirmware/AnimatronicMouthDemo/src/TPP_Animatronic_Global.h)

TIPS ON RECORDING AUDIO CLIPS.

Audio clips for the Animatronic Head may be recorded in your own voice using any voice recording app on your computer or smartphone. Alternatively, synthesized voice clips may be created using on-line text-to-speech services. The recorded clip volume and the enunciation of the words are very important in achieving the best visual effect of the Mouth. This section contains some tips to use when recording your own clips.

All recorded clips should be stored in mp3 format. Online format converters can be used to convert other formats to mp3.

Clip Volume.

Voice clips should be recorded so that the playback volume through the loudspeaker is satisfactory with a “volume” function setting less than 25. The max setting is 30, so this leaves a little room for making the sound louder if necessary.

If a clip created using a voice recording app is too soft, try recording it again, speaking louder or speaking closer to the recording microphone. Otherwise, you might use an audio processing app (e.g. Audicity) to adjust the clip volume. Just be sure that the volume isn’t made so high as to saturate the audio.

Enunciation.

Believe it or not, how you enunciate a voice clip makes a big difference in the visual effect of the Mouth. Be sure to enunciate clearly. In fact, consciously move your jaw when speaking, in accordance with the enunciation of the text. The recorded voice clip may not sound any different but the Mouth jaw movement will present significantly better than if you do not exaggerate your jaw movement when recording.

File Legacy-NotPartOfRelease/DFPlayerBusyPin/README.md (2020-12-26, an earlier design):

# DFPlayerBusyPin

A Particle project named DFPlayerBusyPin.  This program loops through the clips on a DFRobot mini MP3 Player using the Player's BUSY
pin (connected to Photon pin D0) to determine when the preious clip has completed.  I found that it is necessary to wait about 1 second 
after commanding a new clip to be played before testing the BUSY line again (else, clips will be skipped).  The 1 second delay is 
implemented in a non-blocking manner using millis().  This approach seems to be best overall even though it takes up an extra
Photon I/O pin.

## Welcome to your project!

Every new Particle project is composed of 3 important elements that you'll see have been created in your project directory for DFPlayerBusyPin.

#### ```/src``` folder:  
This is the source folder that contains the firmware files for your project. It should *not* be renamed. 
Anything that is in this folder when you compile your project will be sent to our compile service and compiled into a firmware binary for the Particle device that you have targeted.

If your application contains multiple files, they should all be included in the `src` folder. If your firmware depends on Particle libraries, those dependencies are specified in the `project.properties` file referenced below.

#### ```.ino``` file:
This file is the firmware that will run as the primary application on your Particle device. It contains a `setup()` and `loop()` function, and can be written in Wiring or C/C++. For more information about using the Particle firmware API to create firmware for your Particle device, refer to the [Firmware Reference](https://docs.particle.io/reference/firmware/) section of the Particle documentation.

#### ```project.properties``` file:  
This is the file that specifies the name and version number of the libraries that your project depends on. Dependencies are added automatically to your `project.properties` file when you add a library to a project using the `particle library add` command in the CLI or add a library in the Desktop IDE.

## Adding additional files to your project

#### Projects with multiple sources
If you would like add additional files to your application, they should be added to the `/src` folder. All files in the `/src` folder will be sent to the Particle Cloud to produce a compiled binary.

#### Projects with external libraries
If your project includes a library that has not been registered in the Particle libraries system, you should create a new folder named `/lib/<libraryname>/src` under `/<project dir>` and add the `.h`, `.cpp` & `library.properties` files for your library there. Read the [Firmware Libraries guide](https://docs.particle.io/guide/tools-and-features/libraries/) for more details on how to develop libraries. Note that all contents of the `/lib` folder and subfolders will also be sent to the Cloud for compilation.

## Compiling your project

When you're ready to compile your project, make sure you have the correct Particle device target selected and run `particle compile <platform>` in the CLI or click the Compile button in the Desktop IDE. The following files in your project folder will be sent to the compile service:

- Everything in the `/src` folder, including your `.ino` application file
- The `project.properties` file for your project
- Any libraries stored under `lib/<libraryname>/src`

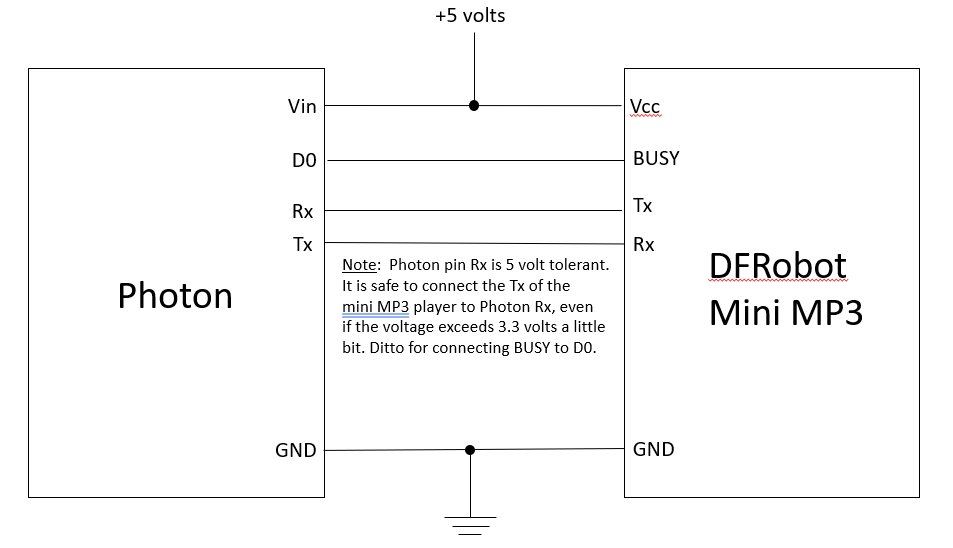
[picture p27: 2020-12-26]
Hardware/MP3 Player Hookup.png

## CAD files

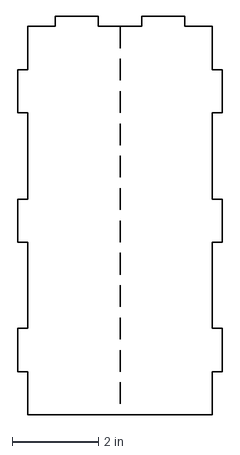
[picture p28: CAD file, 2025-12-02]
Mechanical/armature/puppet_armature_bottom.dxf
4.75 x 9.24 in

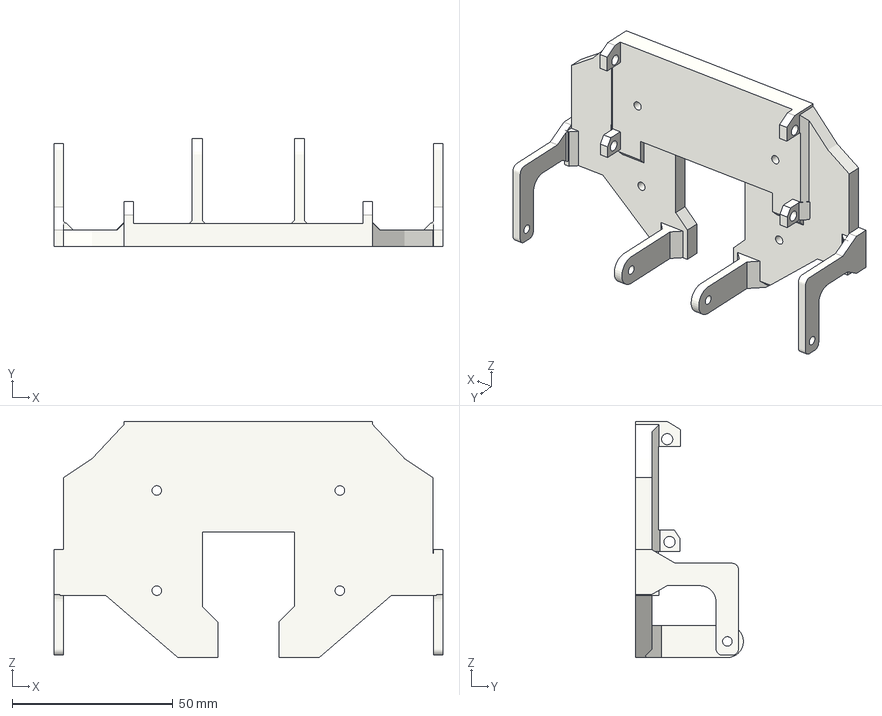
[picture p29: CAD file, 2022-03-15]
Mechanical/EyeMech/Eye Mech Base Modified.3mf
121.1 x 33.5 x 73.5 mm

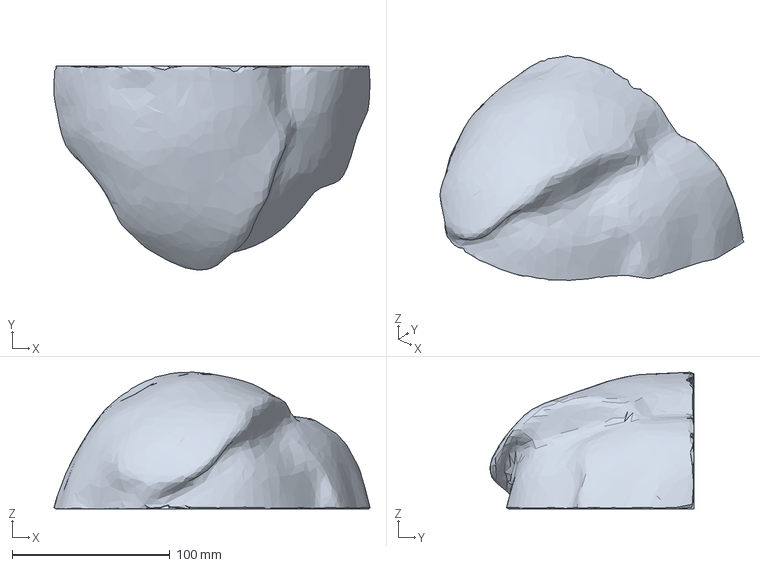
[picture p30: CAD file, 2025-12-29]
Mechanical/Head/head top.3mf
200.5 x 129.5 x 86.7 mm

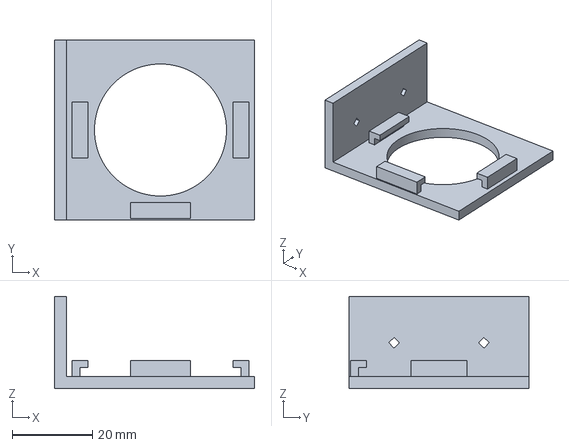
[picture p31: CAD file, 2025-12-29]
Mechanical/MouthMech/speaker_bracket.3mf
50.0 x 45.0 x 23.0 mm

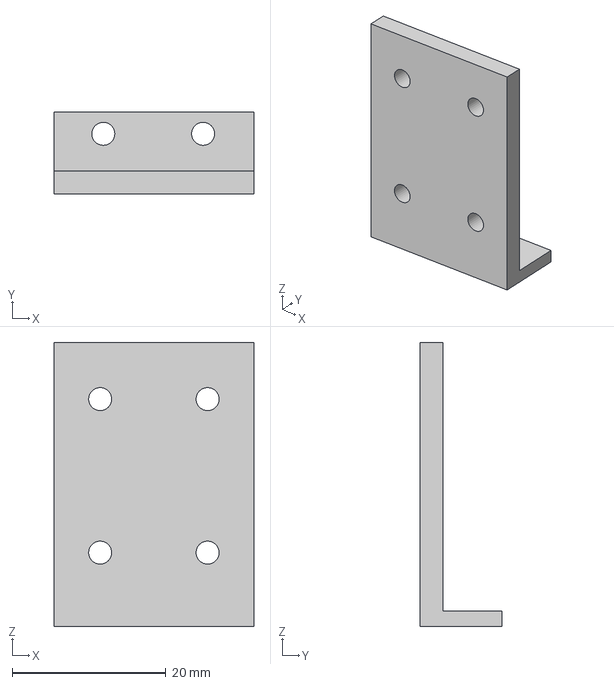
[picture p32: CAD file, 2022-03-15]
Mechanical/PCBMount/eye power mount.3mf
26.0 x 10.7 x 37.0 mm

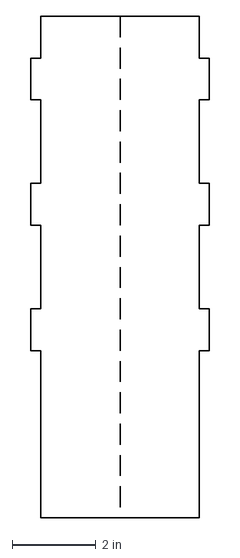
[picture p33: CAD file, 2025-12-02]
Mechanical/armature/puppet_armature_tray_bottom.dxf
4.28 x 12.0 in

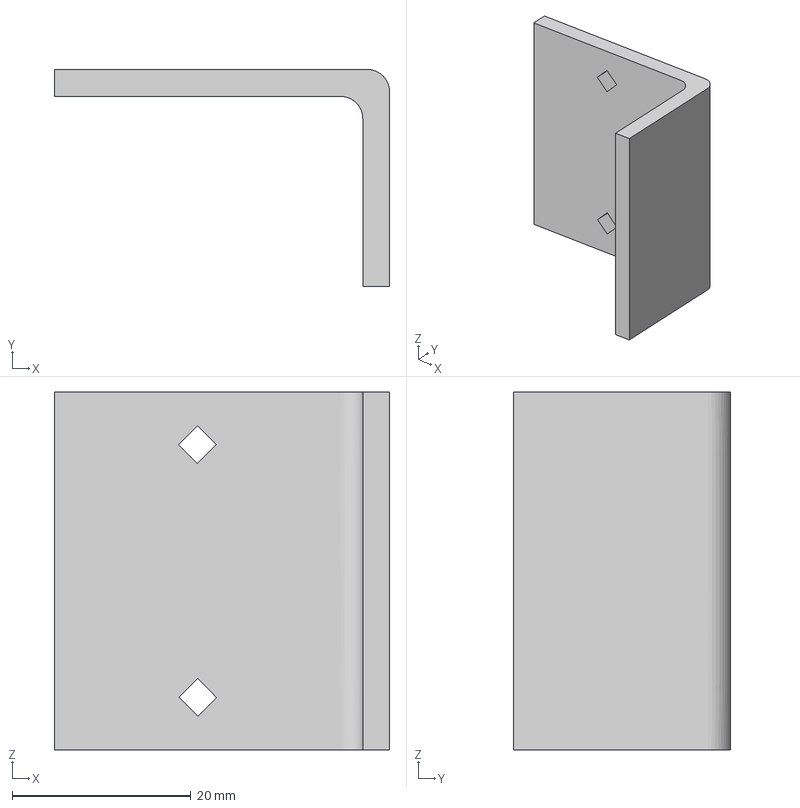
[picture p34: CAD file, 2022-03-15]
Mechanical/Head/Mouth magnet mount.3mf
37.5 x 24.3 x 40.0 mm

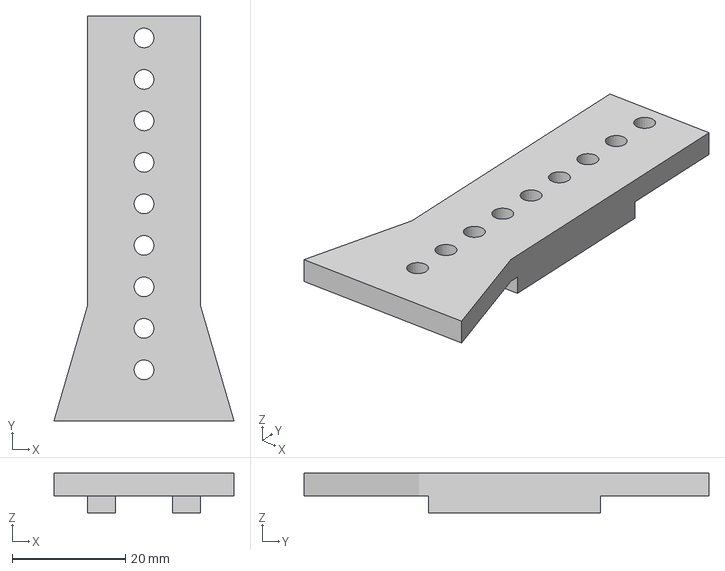
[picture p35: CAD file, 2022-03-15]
Mechanical/MouthMech/standup.3mf
31.8 x 71.5 x 7.00 mm

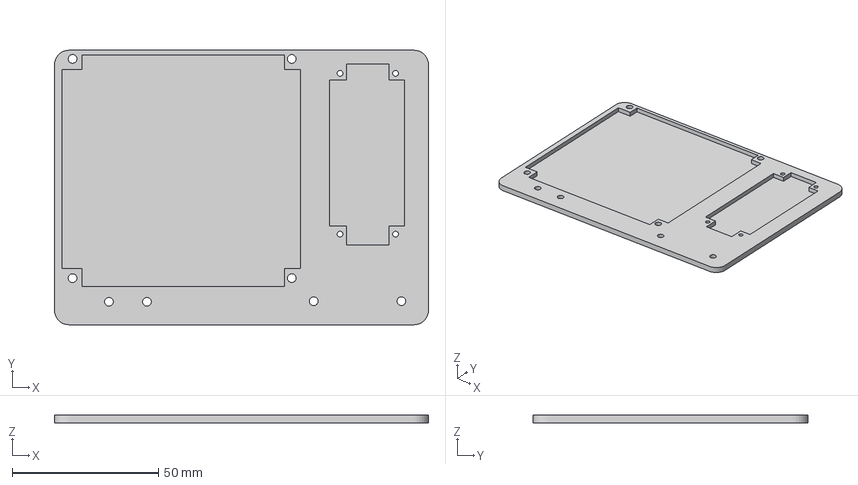
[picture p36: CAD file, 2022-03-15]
Mechanical/PCBMount/eye base plate.3mf
128.0 x 94.0 x 2.60 mm

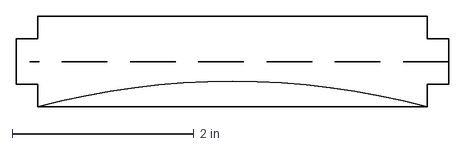
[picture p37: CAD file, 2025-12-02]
Mechanical/armature/puppet_armature_handle.dxf
4.75 x 1.00 in

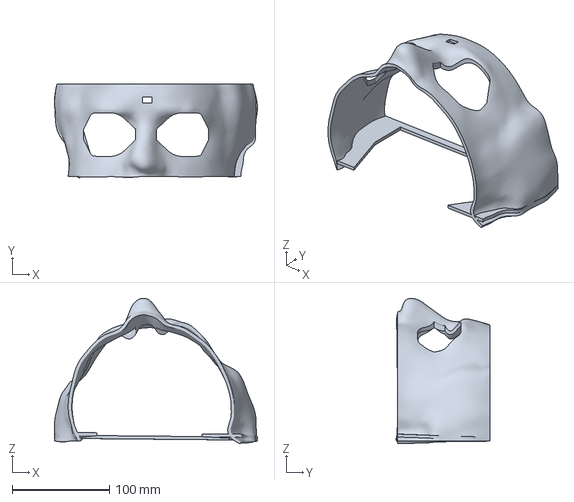
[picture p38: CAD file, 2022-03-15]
Mechanical/Head/Eyes Front.3mf
208.6 x 96.9 x 149.3 mm

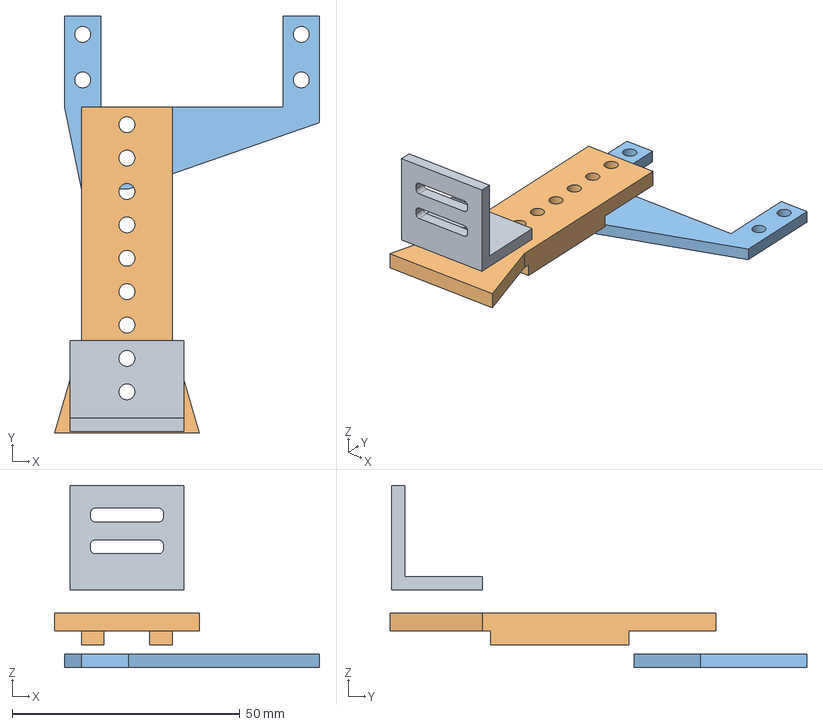
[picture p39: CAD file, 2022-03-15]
Mechanical/MouthMech/jaw servo holder.step
58.2 x 91.5 x 40.0 mm
base
standup
servo holder

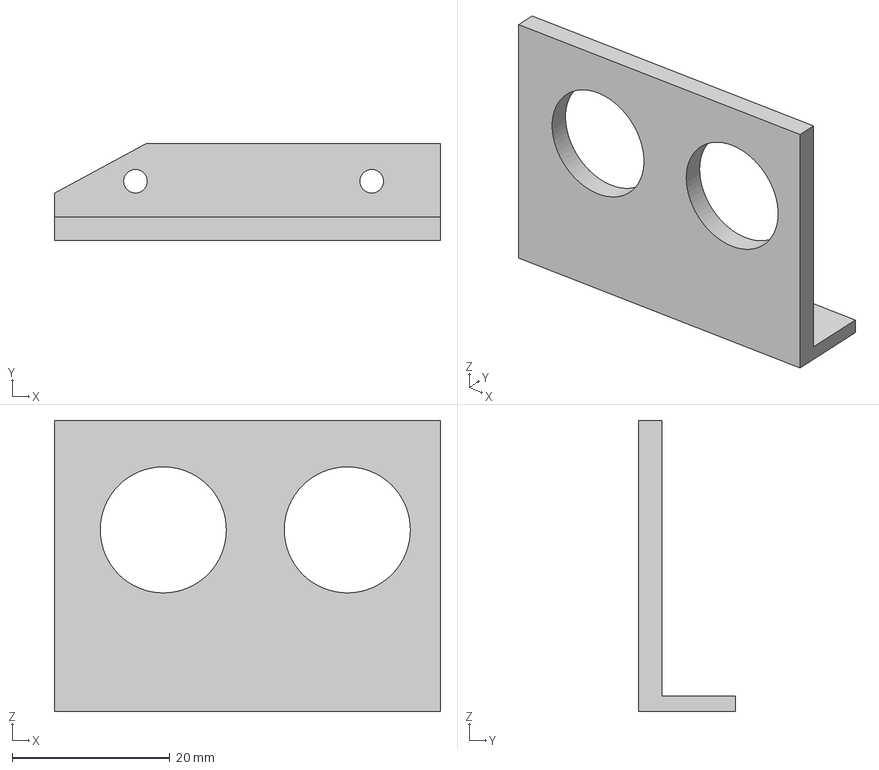
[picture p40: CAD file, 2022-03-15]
Mechanical/PCBMount/mouth switch mount.3mf
49.0 x 12.3 x 37.0 mm

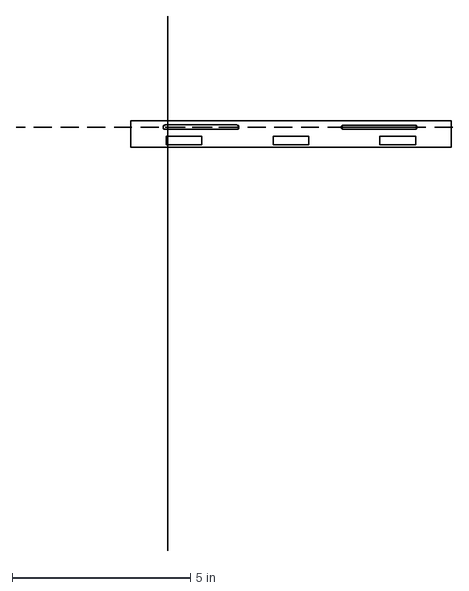
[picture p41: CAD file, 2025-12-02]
Mechanical/armature/puppet_armature_tray_side.dxf
12.2 x 15.0 in

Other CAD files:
Mechanical/Head/mouth.3mf
Mechanical/MouthMech/base.3mf
Mechanical/PCBMount/switch mount.3mf
Mechanical/armature/puppet_armature_side.dxf
Mechanical/Head/Eyes Magnet Mount.3mf
Mechanical/Head/Head Magnet Mount.f3d
Mechanical/Head/Mouth Front.3mf
Mechanical/MouthMech/jaw servo holder.f3d
Mechanical/MouthMech/servo holder.3mf
Mechanical/PCBMount/eye control mount.f3d
Mechanical/PCBMount/eye control mount.step
Mechanical/armature/puppet_armature_back.dxf

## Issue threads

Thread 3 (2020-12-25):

Process "Busy" pin (16) on mini MP3 Player?

BobGlicksman, 2020-12-25:
The processing of status information supplied by the MP3 player via the serial I/O is very complex and confusing -- see DFRPlayerFullTest Clip,ino for more information.  There is a "Busy" pin (pin 16) on the module and indications in the User Manual that reading this pin may be all that is required to know if you can issue a new command to the MP3 Player.  While this will take up an additional Photon I/O pin, this may be a better -- more robust and simpler (less chance of bugs) -- way to handle knowing if a clip has completed.  There is a red LED on the module that lights when a clip is playing and goes out when the clip is done.  It is "assumed" that the BUSY pin follows the LED state.  This should be tested as an alternate method of knowing when a clip has completed playing and that the MP3 module can be commanded to play another clip.

BobGlicksman, 2020-12-26:
A further note on the "busy" pin:  I have read that ending serial commands to the mini MP3 player when it is playing a clip can sometimes cause the playback to be distorted.  This is a further reason to try monitoring the "busy" pin to see if playing has stopped, vs a serial I/O query.

BobGlicksman, 2020-12-27:
An implementation using the BUSY pin on the MP3 player is at: https://github.com/BobGlicksman/Animatronics/tree/main/Software/DFPlayerBusyPin

I found that the busy pin signal works, but only if you wait about one second after commanding a new clip to play before reading the state of the BUSY signal.

Closed 2020-12-27.

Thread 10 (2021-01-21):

Non-linear mouth mapping?

BobGlicksman, 2021-01-21:
As of 1/21/21: The mouth movement circuitry and test firmware appears to be working as designed. The servo-mouth definitely moves in synch with a spoken MP3 clip.  There is a perceptual time lag as you average more samples, as expected.  However, the mouth movement, while in synch with the audio, is not very convincing.  I have noted that a "small" drop in audio sound level results in a seemingly much larger drop in mouth movement.  I THINK that this may be due to the fact that human hearing is logarithmic whereas the sound (envelope) level mapping to servo movement is linear.  Realism MIGHT be improved by some non-linear mapping of sound (envelope voltage) to servo movement which emphasizes low value sound samples more than high volume sound samples.  Perhaps something like a 4 point linear mapping of A/D values to servo commands would work:
1. Divide the mapping range (High - Low) of input A/D values into 4 equal sub-ranges.
2. Multiply the lower range sound values by 4, the mid-low range sound values by 3, the mid-high range sound values by 2, and the high range sound values by 1.
3.  scale the mapped values to the servo movement range.

BobGlicksman, 2021-01-22:
I added a call to a non-linear scaling function (firmware v1.2).  This scaling function uses the sqrt() function from the Math library - mostly for convenience.  It does appear to add realism to the moth movement.  However, there still seems to be some tendency for the mouth to not pick up the last syllable all of the time.  I don't know why this is -- it is not simply a matter of voice volume dropoff.  Perhaps the mini-MP3 BUSY line sometimes drops a little too soon?  Perhaps the last bit is on the wrong track of the MP3 file (not the one playing through the analog processor), albeit I think that the recording is monaural.

jschrempp, 2022-10-21:
I added nlp2 with this algorithm and it seems to look good. Unsure why it does the job better than nlp1.

      averagedData = sqrt(averagedData) / sqrt(maxValue) * maxValue;

jschrempp, 2022-11-04:
I think we can close this issue now.

BobGlicksman, 2022-11-04:
Agreed.

-----Original Message-----
From: Jim Schrempp ***@***.***>
To: BobGlicksman/Animatronics ***@***.***>
Cc: Bob Glicksman ***@***.***>; Author ***@***.***>
Sent: Fri, Nov 4, 2022 1:36 pm
Subject: Re: [BobGlicksman/Animatronics] Non-linear mouth mapping? (#10)

I think we can close this issue now.—
Reply to this email directly, view it on GitHub, or unsubscribe.
You are receiving this because you authored the thread.Message ID: ***@***.***>

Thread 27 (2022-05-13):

Restructure Animatronic eyes code

BobGlicksman, 2022-05-13:
The current code in AnimatronicEyes.ino has a time test for most of the processing in loop():

if ( (millis() - lastEyeUpdateMS) > TOF_SAMPLE_TIME) { ... }

Every time that this times criteria is met, theTOF.getPOI() is called to get new TOF sensor data.  This timed approach does not know if the TOF actually took new readings or not, so processing is wasted if the TOF sensor did not take new readings.  The sensor readings data is obtained inside this if() statement by theTOF.getPOI() function call; this function being defined in TPP_TOF.cpp.  The return value from getPOI() is void.  getPOI() checks the TOF sensor library function myImager.isDataReady() to see if the image has taken a new reading, but this result is only used to skip reading and processing new data and does not report the availability of new sensor data (or not) up to loop().  Therefore, timed polling in loop() wastes some processing time by periodically polling the returned data struct, only to find out that the data hasn't changed.

It is proposed to add a bool or int return value to getPOI() that indicates the status of the sensor library isDataReady() function call.  In loop(), within AnimatronicEyes.ino, we would dispense with the timed polling of the data and simply call getPOI() on every loop and test the return value to see if there is actual new data to process.  If not, we skip down to the bottom of loop().

This change should clean up the logic of the code a little and will eliminate some unnecessary processing.  The code change is not expected to improve the performance in any significant way.

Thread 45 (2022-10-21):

ENH: Idle sensor recalibration

jschrempp, 2022-10-21:
When the Eyes code starts up it takes a reading from the 8x8 TOF sensor. This reading is then used as a background calibration. When sensor region values differ from this calibration frame we assume someone is standing there.

In operation the puppet head is often moved accidentally, or by a person who is looking into its inner workings. When this happens we need to reboot the Eyes code to get a new calibration frame.

With this enhancement I propose that after some period of time where the TOF regions have not changed, we take that frame as a new background calibration.

How long should this be? It could be rather short. The TOF sensor is very sensitive to changes (on the order of 1 mm); it is hard to stand in front of it without triggering a change. We will have to experiment, but it might be that 5 seconds without a change is enough to qualify for a new calibration frame.

What tolerance should we have to sensor region changes? If the sensor field is completely open, then changes are few. If the sensor field has some stationary objects in it, then we can get spurious value changes; we have attributed these to reflectance. We should examine what these spurious reports look like and compare them to the case when a human is actually in the field of view. It may be possible to determine these different cases. For example, spurious reports may tend to come in just one region at a time whereas it is hard for a person to disturb only one region.

BobGlicksman, 2022-10-22:
The main issue that I see with this proposal is that the background calibration must be the "background".  How can we be sure that this automatic recalibration is, in fact, sensing the background?  What if the head is on a table at MN and someone moves a piece of equipment in front of it and then leaves the equipment there for a little while, e.g. to clear space to move the equipment into a permanent location.  The calibration will see the equipment as background, then the equipment is moved and people coming into the TOF fov are no longer sensed because they are further away.

Here is an alternative proposal:  we have pin A5 unused in the PCB.  Perhaps we put a button on this pin -- press the button to recalibrate the TOF without the need to reboot the board?  This way, we ensure that the head is again set up in the place where we want to calibrate.

jschrempp, 2022-10-22:
I think I understand your point, but if the equipment was later moved away, then the auto-calibration would deal with that at the next auto-calibrate interval. That might be just five seconds.

BobGlicksman, 2022-10-22:
It won't hurt to try the auto-recalibration and see how it works out.  If we find operational problems, we can always back auto-recalibration out and put in a calibrate button.

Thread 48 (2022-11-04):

ENH: Add start up done event

jschrempp, 2022-11-04:
When the Eyes have finished loading the TOF sensor and taken the first calibration frame, send and event to the Mouth so it can speak something like "system ready".

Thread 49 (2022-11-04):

Spurious hello/goodby events when no motion in frame

jschrempp, 2022-11-04:
When the field of view is unchanging, the Eyes will still occasionally emit an TOF event for someone entering the field of view. We've seen that there are spurious readings in any given cell. We've tried to filter that out by requiring several adjoining cells to go active at the same time, our theory is that rarely will a real human in the FOV register in just one cell.

The idea is to add some temporal filtering to the code so that an even is only triggered if something in the FOV remains there for some short period of time.

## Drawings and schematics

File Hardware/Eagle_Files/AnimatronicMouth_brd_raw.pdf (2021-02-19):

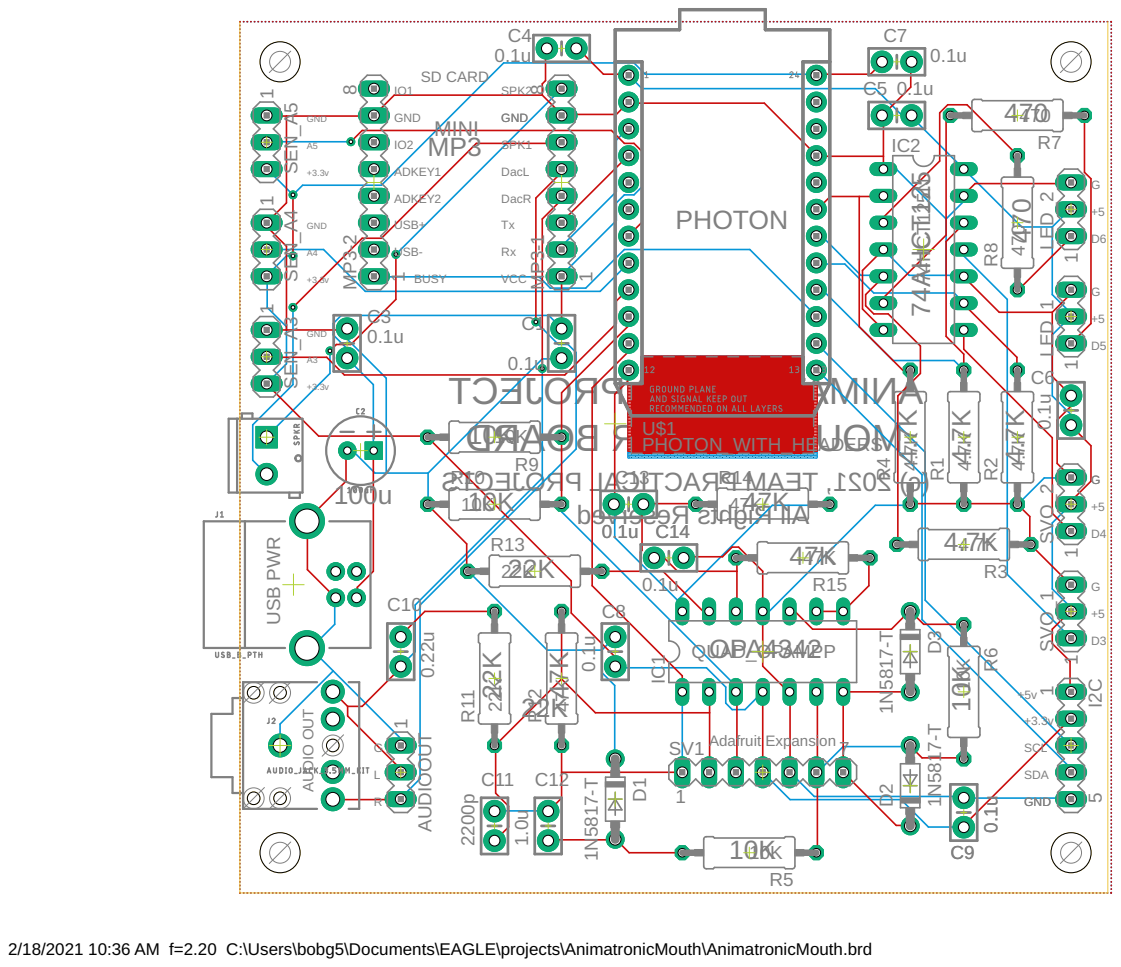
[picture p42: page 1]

2/18/2021 10:36 AM f=2.20 C:\Users\bobg5\Documents\EAGLE\projects\AnimatronicMouth\AnimatronicMouth.brd

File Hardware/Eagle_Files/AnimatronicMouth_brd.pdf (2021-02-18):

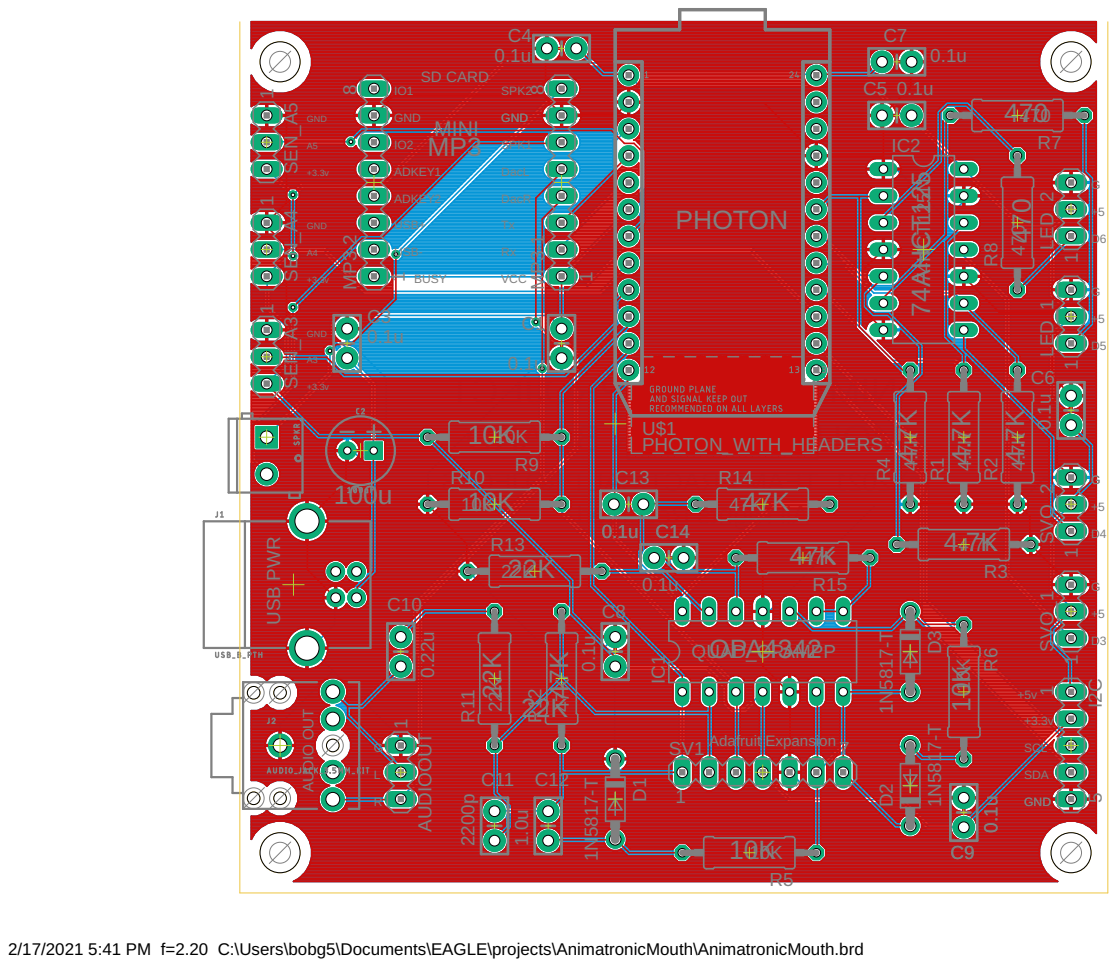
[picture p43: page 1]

2/17/2021 5:41 PM f=2.20 C:\Users\bobg5\Documents\EAGLE\projects\AnimatronicMouth\AnimatronicMouth.brd

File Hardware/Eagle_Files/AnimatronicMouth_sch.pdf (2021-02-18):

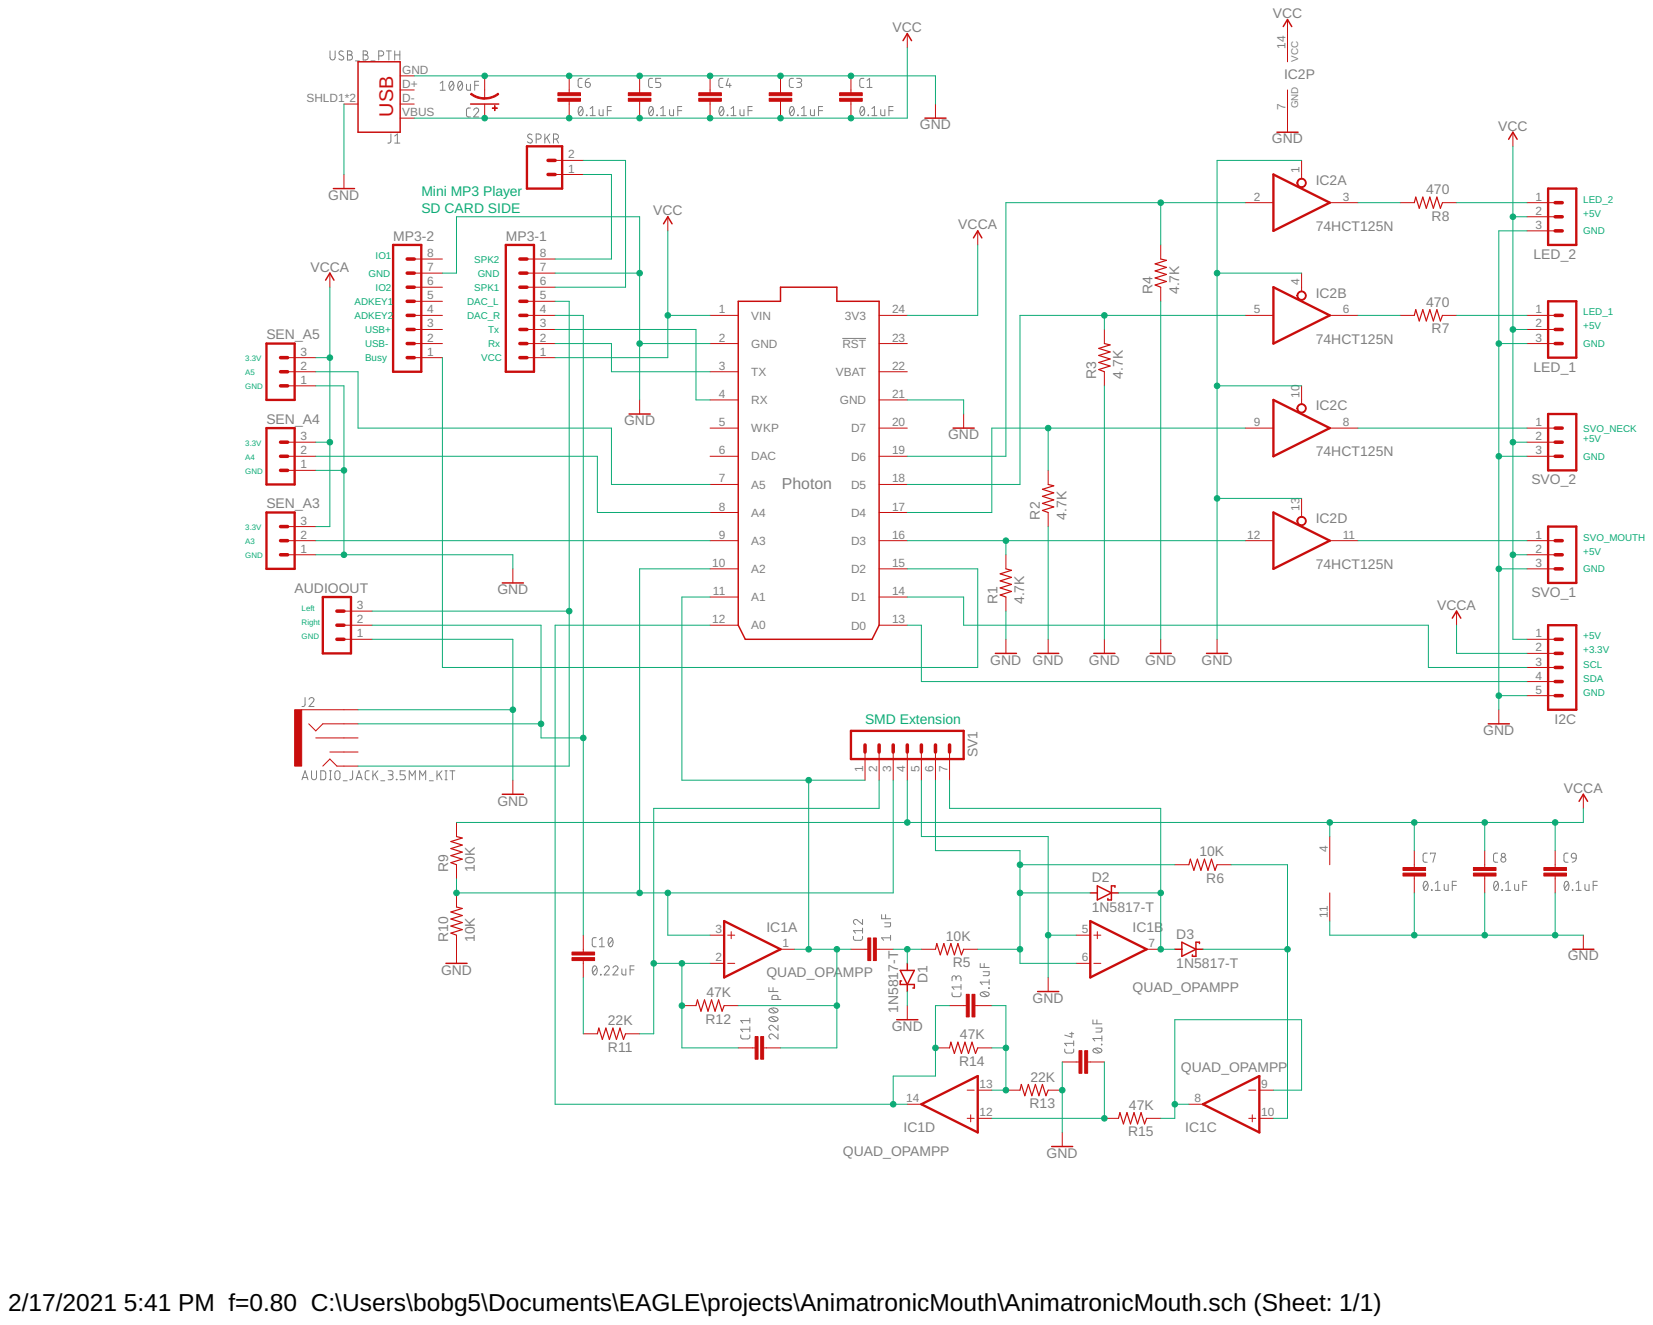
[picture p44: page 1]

2/17/2021 5:41 PM f=0.80 C:\Users\bobg5\Documents\EAGLE\projects\AnimatronicMouth\AnimatronicMouth.sch (Sheet: 1/1)

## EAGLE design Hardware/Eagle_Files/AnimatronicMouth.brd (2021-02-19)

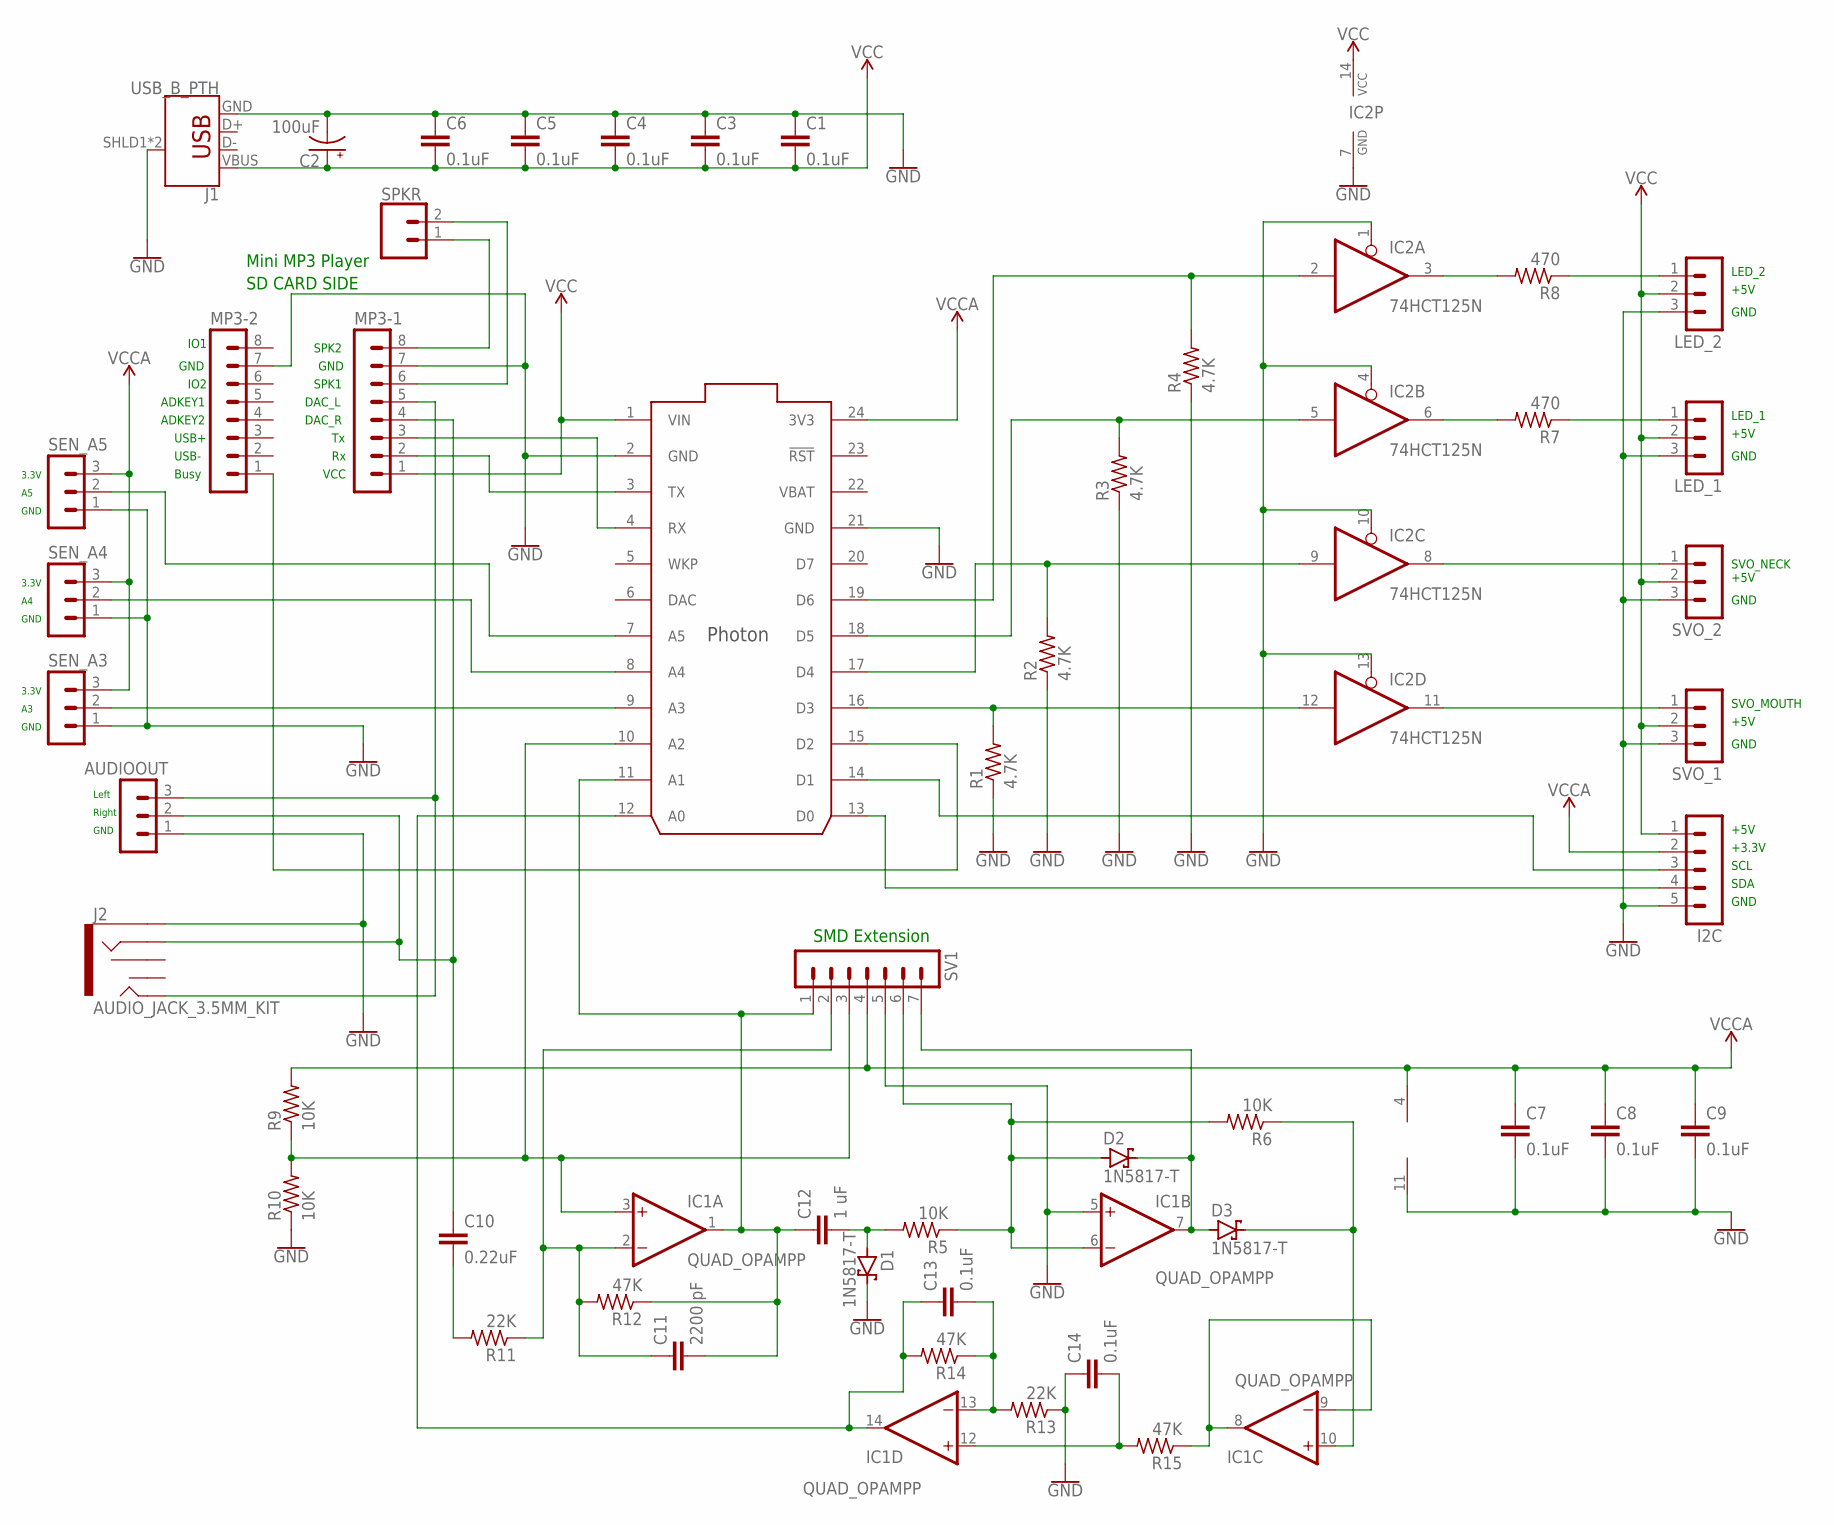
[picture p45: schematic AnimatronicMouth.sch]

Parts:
AUDIOOUT: MA03-1
C1, C3, C4, C5, C6, C7, C8, C9, C13, C14: 0.1uF; CAP-PTH-SMALL-KIT
C2: 100uF; CPOL-RADIAL-2.5MM-6.5MM
C10: 0.22uF; CAP-PTH-SMALL-KIT
C11: 2200 pF; CAP-PTH-SMALL-KIT
C12: 1 uF; CAP-PTH-SMALL-KIT
D1, D2, D3: 1N5817-T; DO41-7.6
I2C: MA05-1
IC1: QUAD_OPAMPP; DIL14
IC2: 74HCT125N; DIL14
J1: USB_B_PTH; USB-B-PTH
J2: AUDIO_JACK_3.5MM_KIT; AUDIO-JACK-KIT
LED_1, LED_2: MA03-1
MP3-1, MP3-2: MA08-1
R1, R2, R3, R4: 4.7K; 0309/12
R5, R6, R9, R10: 10K; 0309/12
R7, R8: 470; 0309/12
R11, R13: 22K; 0309/12
R12, R14, R15: 47K; 0309/12
SEN_A3, SEN_A4, SEN_A5: MA03-1
SPKR: CONN_023.5MM; SCREWTERMINAL-3.5MM-2
SV1: MA07-1
SVO_1, SVO_2: MA03-1
U$1: PHOTON_WITH_HEADERS; PHOTON

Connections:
GND: AUDIOOUT.1, C1.1, C2.2 (-), C3.1, C4.1, C5.1, C6.1, C7.2, C8.2, C9.2, C14.1, D1.C, I2C.5, IC1.5 (+IN), IC1.11 (V-), IC2.1 (OE), IC2.4 (OE), IC2.7 (GND), IC2.10 (OE), IC2.13 (OE), J1.GND, J1.SHLD1 (SHIELD), J1.SHLD2 (SHIELD), J2.SLEEVE, LED_1.3, LED_2.3, MP3-1.7, MP3-2.7, R1.1, R2.1, R3.1, R4.1, R10.1, R13.1, SEN_A3.1, SEN_A4.1, SEN_A5.1, SV1.5, SVO_1.3, SVO_2.3, U$1.2 (GND), U$1.21 (GND)
unnamed: IC2.12 (I), R1.2, U$1.16 (D3)
unnamed: IC2.5 (I), R3.2, U$1.18 (D5)
unnamed: IC2.9 (I), R2.2, U$1.17 (D4)
unnamed: IC2.2 (I), R4.2, U$1.19 (D6)
unnamed: IC2.11 (O), SVO_1.1
unnamed: LED_2.1, R8.1
unnamed: IC2.8 (O), SVO_2.1
unnamed: LED_1.1, R7.1
unnamed: IC2.6 (O), R7.2
unnamed: I2C.4, U$1.13 (D0)
unnamed: IC2.3 (O), R8.2
unnamed: MP3-1.6, SPKR.2
unnamed: C11.2, C12.1, IC1.1 (OUT), R12.1, SV1.1, U$1.11 (A1)
unnamed: IC1.3 (+IN), R9.1, R10.2, SV1.3, U$1.10 (A2)
unnamed: AUDIOOUT.2, C10.1, J2.RING, MP3-1.4
unnamed: C12.2, D1.A, R5.2
unnamed: D2.A, IC1.6 (-IN), R5.1, R6.2, SV1.6
unnamed: D2.C, D3.A, IC1.7 (OUT), SV1.7
unnamed: C13.1, IC1.14 (OUT), R14.2, U$1.12 (A0)
unnamed: C10.2, R11.2
unnamed: C11.1, IC1.2 (-IN), R11.1, R12.2, SV1.2
unnamed: MP3-1.2, U$1.3 (TX)
unnamed: MP3-1.3, U$1.4 (RX)
unnamed: MP3-2.1, U$1.15 (D2)
unnamed: AUDIOOUT.3, J2.TIP, MP3-1.5
unnamed: I2C.3, U$1.14 (D1)
unnamed: MP3-1.8, SPKR.1
unnamed: SEN_A5.2, U$1.7 (A5)
unnamed: D3.C, IC1.10 (+IN), R6.1
unnamed: SEN_A3.2, U$1.9 (A3)
unnamed: SEN_A4.2, U$1.8 (A4)
unnamed: C13.2, IC1.13 (-IN), R13.2, R14.1
unnamed: C14.2, IC1.12 (+IN), R15.2
unnamed: IC1.8 (OUT), IC1.9 (-IN), R15.1
VBAT: U$1.22 (VBAT)
VCC: C1.2, C2.1 (+), C3.2, C4.2, C5.2, C6.2, I2C.1, IC2.14 (VCC), J1.VBUS, LED_1.2, LED_2.2, MP3-1.1, SVO_1.2, SVO_2.2, U$1.1 (VIN)
VCCA: C7.1, C8.1, C9.1, I2C.2, IC1.4 (V+), R9.2, SEN_A3.3, SEN_A4.3, SEN_A5.3, SV1.4, U$1.24 (3V3)

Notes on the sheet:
VCC
DAC_R
DAC_L
SPK1
GND
SPK2
Busy
USB-
USB+
ADKEY2
ADKEY1
IO2
IO1
SD CARD SIDE
Mini MP3 Player
Right
Left
SDA
SCL
+3.3V
+5V
3.3V
SVO_MOUTH
SVO_NECK
LED_1
LED_2
SMD Extension

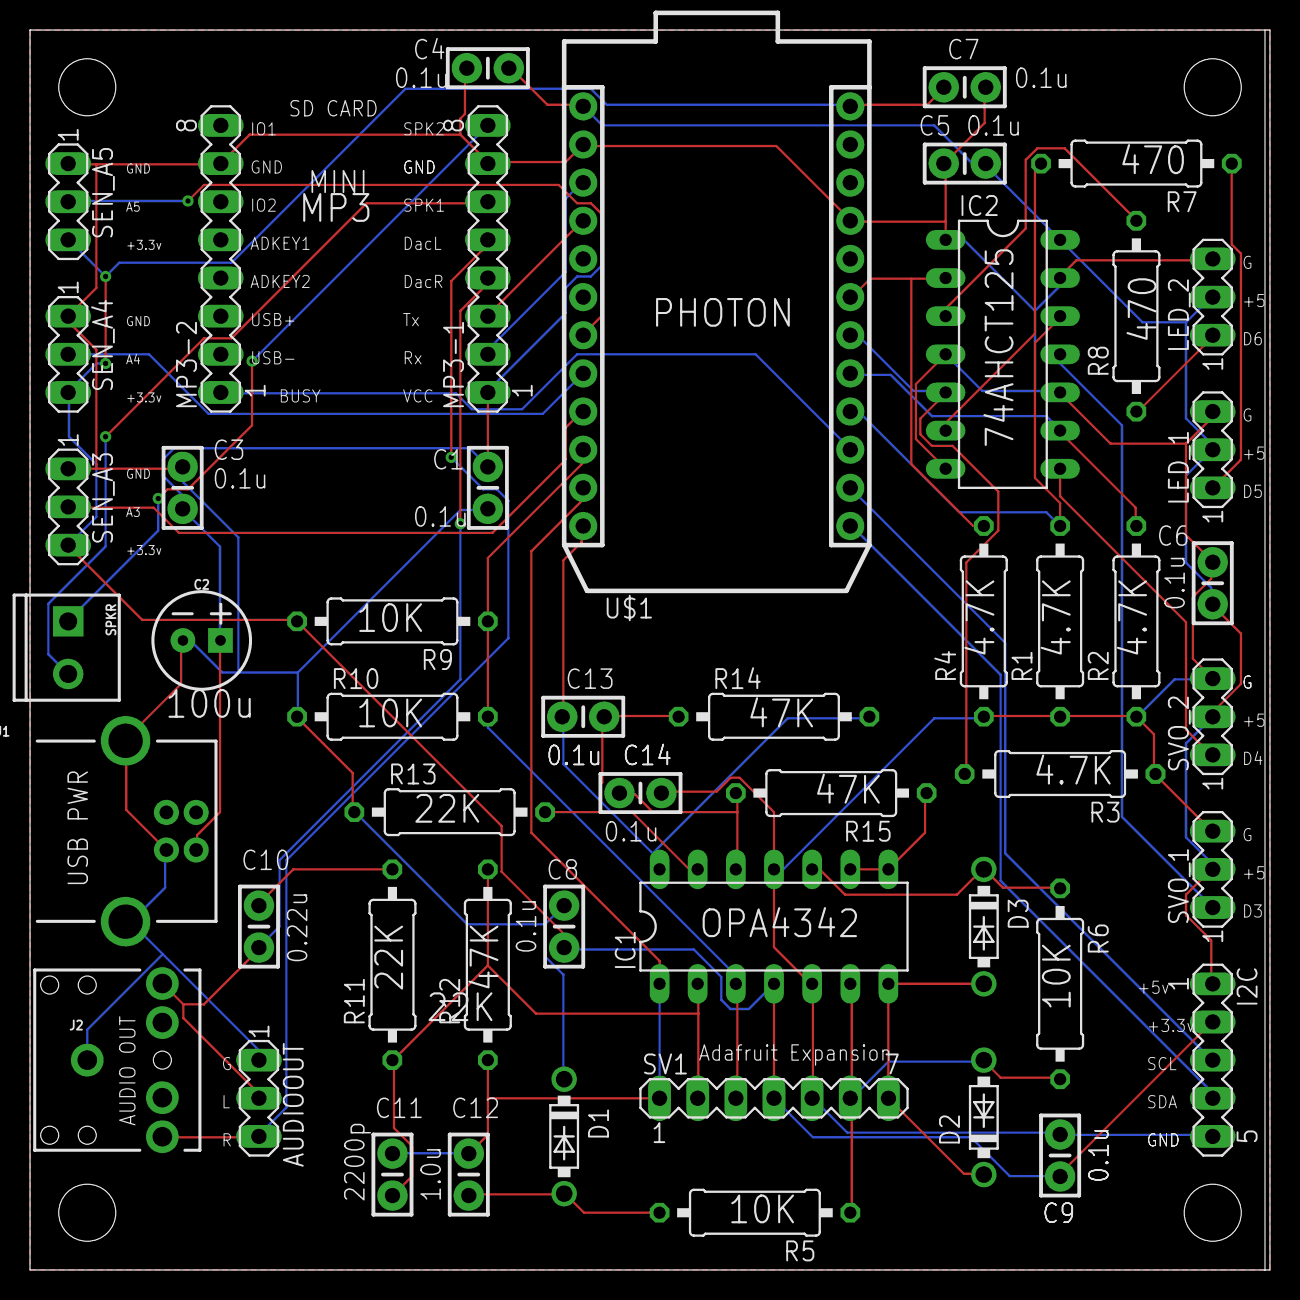
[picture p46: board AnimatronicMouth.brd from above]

Board: 2 copper layers, 82.5 x 82.5 mm, 50 parts (0 on the bottom side), 37 nets.

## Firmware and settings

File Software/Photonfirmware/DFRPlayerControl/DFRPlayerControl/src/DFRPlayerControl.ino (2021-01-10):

/***************************************************
DFPlayerControl.ino:  Program that plays a clip from
the DFRobot miniMP3 player continuously (over and over).
The clip is selected via Particle.function() so that it
can be selected from the Particle Console.  This program
is intended for testing the analog processing circuitry 
that has been designed for the Animatronics project.

This program tests the BUSY pin on the MP3 player in 
order to determine that a clip is finished playing before 
repeating it.  On each repeat, a global variable determines
the clip that is to be played.  To change the clip, use
the cloud function.

Experimentation has revealed the following:
It is necessary to wait about 1 second after starting to play a clip
before testing the BUSY line to see that the MP3 player is actually
busy.  A non-blocking 1 second timer is used in this program.

This software is based upon "DFPlayerBusyPin.ino" which was used to
determine how to use the miniMP3 Player's BUSY pin.  The BUSY
pin is connected to pin D0 on the Photon.  Photon Tx is connected
to miniMP3 Rx and Photon Rx is connected to miniMP3 Tx.  The Photon
Serial1 port is thereby used to communicate with the miniMP3 player
 
Author: Bob Glicksman 
Date: 1/10/21
Version 1.0
*****************************************************/

#include <DFRobotDFPlayerMini.h>  // MP3 player library
DFRobotDFPlayerMini myDFPlayer;

const int BUSY_PIN = D0;
const int LED_PIN = D7;
const unsigned long BUSY_TIMER = 1000;
const int LAST_CLIP_NUM = 13;

int clip = 0; // the clip to play
int volume = 30;   // the mini MP3 player volume

void setup()
{
  Serial1.begin(9600);  // mini MP3 player conected using Serial1; Tx/Rx pins on Photon

  // debug: enable usb serial port and print mini MP3 status
  Serial.begin(9600);   // use Putty for control and status via Serial (USB) port
  Serial.println();
  Serial.println(F("DFRobot DFPlayer Mini Demo"));
  Serial.println(F("Initializing DFPlayer ... (May take 3~5 seconds)"));
  
  if (!myDFPlayer.begin(Serial1)) {  //Use Photon Serial1 to communicate with mp3 player
    Serial.println(F("Unable to begin:"));
    Serial.println(F("1.Please recheck the connection!"));
    Serial.println(F("2.Please insert the SD card!"));
    while(true);  // hang up here to clear out hardware issue
  }
  Serial.println(F("DFPlayer Mini online."));

  pinMode(BUSY_PIN, INPUT); // setup the busy status indicator
  pinMode(LED_PIN, OUTPUT); // the D7 led
  digitalWrite(LED_PIN, LOW);



  // register the cloud function that selects the clip to play
  Particle.function("clip number", clipNum);

  // register the cloud function that selects the volume
  Particle.function("volume", clipVolume);

  delay(5000);  // delay to get putty going

} // end of setup()

void loop() {
  static unsigned long busyDelay = millis();

  digitalWrite(LED_PIN, HIGH); // indicate ready via D7 LED

  // non-blocking timer
  if( (millis() - busyDelay ) >= BUSY_TIMER) {

    // test the busy pin to see if the MP3 player is ready to play a new track
    if(digitalRead(BUSY_PIN) == HIGH) { // HIGH means ready, LOW means busy
      if( (clip > 0) && (clip <= LAST_CLIP_NUM)) {
        Serial.print("\nPlaying clip: "); 
        Serial.println(clip);

        myDFPlayer.volume(volume);  //Set volume value. From 0 to 30
        myDFPlayer.play(clip);  // play the next track

      }
      busyDelay = millis(); // update the busy timer
    }
  }

} // end of loop()

// the cloud function to select the next clip.  0 = no clip
int clipNum(String clipNumber) {
  clip = clipNumber.toInt(); // set the global variable to the next clip number
  return 0;
} // end of clipNum()

// the cloud function to select the clip volume (0 - 30)
int clipVolume(String clipVol) {
  volume = clipVol.toInt(); // set the global variable to the next clip number
  return 0;
} // end of clipVol()

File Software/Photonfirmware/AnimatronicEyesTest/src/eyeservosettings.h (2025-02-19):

/*
 * eyeservosettings
 * Part of the animatronic exploration of Team Practical Projects
 * https://github.com/TeamPracticalProjects
 * 
 * These are the settings that are used to position the eye control
 * servos. They depend on your particular eye mechanism, the servos you
 * use and how the horns are attached to the servo shafts.
 * 
 * You should run the AnimatronicEyesCalibration.ino firmware to determine
 * the values to put in this file.
 * 
 * You can select the set of values to use by uncommenting a #define
 *    
 */ 

//#define SETTINGS_JIMS
#define SETTINGS_BOBG


// Servo Positions
// Use the calibration test code to figure the correct values for each.
// THE CALIBRATION TEST WILL PRINT A SET OF DEFINES THAT YOU CAN COPY
// AND PASTE OVER THE ONES BELOW. 
// -------------------------------------------------------------------
// -------------------------------------------------------------------

#ifdef SETTINGS_JIMS
 
  #define X_POS_MID 400
  #define X_POS_LEFT_OFFSET 141
  #define X_POS_RIGHT_OFFSET -121

  #define Y_POS_MID 407
  #define Y_POS_UP_OFFSET 98
  #define Y_POS_DOWN_OFFSET -82

  #define LEFT_UPPER_CLOSED 486
  #define LEFT_UPPER_OPEN 287

  #define LEFT_LOWER_CLOSED 258
  #define LEFT_LOWER_OPEN 450

  #define RIGHT_UPPER_CLOSED 261
  #define RIGHT_UPPER_OPEN 469

  #define RIGHT_LOWER_CLOSED 509
  #define RIGHT_LOWER_OPEN 256

#endif

#ifdef SETTINGS_BOBG

#define X_POS_MID 373
#define X_POS_LEFT_OFFSET 96
#define X_POS_RIGHT_OFFSET -82

#define Y_POS_MID 440
#define Y_POS_UP_OFFSET 69
#define Y_POS_DOWN_OFFSET -108

#define LEFT_UPPER_CLOSED 500
#define LEFT_UPPER_OPEN 281

#define LEFT_LOWER_CLOSED 281
#define LEFT_LOWER_OPEN 538

#define RIGHT_UPPER_CLOSED 255
#define RIGHT_UPPER_OPEN 510

#define RIGHT_LOWER_CLOSED 536
#define RIGHT_LOWER_OPEN 266

#endif



// -------------------------------------------------------------------
// -------------------------------------------------------------------

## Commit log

2020-12-19 Create repository
    Added files for testing.
    [Welcome_Waveform_High_Data.xlsx]
2020-12-24 Update MP3 Player Hookup.png
    Removed 4.7K resistor between MP3 Tx and Photon Rx because Photon Rx is 5 volt tolerant. I was concerned about the MP3 module internal regulator producing a highr (than 3.3 volt) signal from the 5 volt power supply, but the 5 volt tolerance of Rx renders this issue moot.
2020-12-26 Busy Pin Test program
    This program uses the BUSY pin in the MP3 Player (connected to Photon D0) to determine when the Player is not busy (when a clip is complete). I found that it is necessary to provide a delay of about 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
2020-12-30 Analog Processing V2
    New V2 circuit with analysis simulation data.
2020-12-30 Update Analog_Processor_V2_Analysis.pptx
    Added envelope filter freq response to ppt
2021-01-10 reverted servo numbers from test values
2021-01-14 Create Photo_of_V2_circuit_in_breadboad.jpg
    Breadboard of V2 analog processing circuit. This breadboard circuit has been tested with the audio test files played through the moni MP3 player, controlled by a Photon. The output was verified using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
2021-01-16 test program to read analog and control servo
    This test program allows the user (via the Particle console) to set the mini MP3 player volume and clip number and play the selected clip. It samples the analog processing circuit envelope output eve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
2021-01-16 Added video clips
    Welcome_10ms_Samples.mp4 commands the servo every 10 ms. Welsome_20ms_Samples.mp commands the servo every 20 ms (averaging every 2 samples).
2021-01-16 Now with sample scene list and better comments
2021-01-17 SoundMountIntegration V1.1
    Added constrain() so that servo doesn't peg. Toggle the D7 LED on each write to the servo so that the writing rate can be verified on a scope.
    [SoundMouthIntegrationTest.ino]
2021-01-18 move to better init PWM library
2021-02-12 Changed Servo Limits
    Changed servo limits for Jim's V1 "mouth"
2021-02-17 Added Eagle PCB Files
    [AnimatronicMouth.brd, AnimatronicMouth.sch]
2021-02-18 Updated Eagle Files
    Corrected MP3 width
    [AnimatronicMouth.brd]
2021-02-18 Posted correct eagle files
    [AnimatronicMouth.brd]
2021-02-19 Updated Eagle Files
    Corrected Board Outline problem. This design is released for production.
    [AnimatronicMouth.brd]
2021-03-08 Updated firmware
    Servo limits for the latest mouth version
2021-03-11 Updated Firmware (constants)
    Constants only; testing PCB for mouth and my eye setup.
2021-03-14 Update SoundMouthIntegrationTest.ino
    Updated comments up front of the code to reflect the PCB and latest changes.
2021-03-20 Changed Photons for PC board testing
    There is no change to the code or the configuration other than changing Photons to get the code running on two PCBs,
2021-04-09 Update AnimatronicEyes.ino
    Changed calibration values for my eye mechanism.
2021-04-18 Update MN_Demo_Mouth.ino
    Incorporated the busy pin testing with busy hold delay.
2021-04-20 pre-release v0.1
    The code is complete and tested except for implementation of the pause button.
2021-04-21 Update MN_Demo_Mouth.ino
    Added button processing state machine and debounced button pressed function. Need to use this function to implement pause state.
2021-10-31 1.4 kill switch; better wake up.
2021-11-06 Create adafruit_16channelServo_schem.png
    Added Adafruit 16 channel servo board schematic to hardware folder.
2021-11-15 Recalibrated eyes
    Used the latest version of the calibration code to recalibrate the eyes. Pasted the new calibration values into the eyes animation code.
2021-12-29 added structure for TOF sensor
2022-01-16 Update eyeservosettings.h
    re-calibrated the eyes
2022-02-17 Update MN_Demo_Mouth.ino
    corrected typos
    [MN_Demo_Mouth.ino]
2022-02-17 Update MN_Demo_Mouth.ino
    Added error detection for out of range enumerated value.
    [MN_Demo_Mouth.ino]
2022-03-15 added mechanical files
    [Eye Mech Base Modified.3mf, Eyes Front.3mf, Eyes Magnet Mount.3mf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]
2022-03-21 Update eyeservosettings.h
    The latest calibration
2022-03-22 Update MN_Demo_Mouth.ino
    changed mouth servo limit constants for new 3D printed mouth bracket
2022-03-22 Update MN_Demo_Mouth.ino
    Update with new mouth limit constants for newly positioned mouth servo.
2022-04-14 Update MN_Demo_Mouth.ino
    Slight changes to mouth servo limits after remounting mouth servo with velcro.
2022-05-06 New servo settings
    I repaired my eye mechanism and therefore recalibrated.
2022-05-13 Update AnimatronicEyes.ino
    bumped the version to 1.8 and fixed a minor typo in a comment.
    [AnimatronicEyes.ino]
2022-05-28 Update MN_Demo_Mouth.ino
    Implemented #define for different mouth calibrations for Jim and for Bob
2022-10-05 personalities. mouth calibration cloud func.
2022-10-05 bug fix line 174. numClips was one too large
    [MN_Demo_Mouth.ino]
2022-10-21 won't play same clip twice in a row
    [MN_Demo_Mouth.ino]
2022-11-04 fix for corruption in personalities
    [MN_Demo_Mouth.ino]
2022-11-25 temporal filtering
2022-11-29 better temporal filtering
2022-11-29 more of temporal filtering
2022-11-29 added cloud reset function for testing
    [AnimatronicEyes.ino]
2022-11-30 temporal filter requires same x,y
2022-11-30 1.9 with multiframe calibration and xy temporal
2022-12-01 fix so mouth gets goodbye events
    [AnimatronicEyes.ino]
2022-12-02 fix for goodbye while standing in front of head
    [AnimatronicEyes.ino, TPP_TOF.cpp]
2022-12-02 disable the spatial jitter
    [TPP_TOF.cpp]
2022-12-07 bug fix for repeated hello/goodbye
    [AnimatronicEyes.ino]
2022-12-08 bug fix: state machine conforms to diagram
    [AnimatronicEyes.ino]
2023-01-04 Recalibrated my eyes servos
    Recalibrated after repair
2025-02-08 Update README.md
    Updated this file to reflect the current state of the project,
2025-02-10 Updated eye calibration
    Re-calibrated the eyes. Also documented the calibration procedure.
2025-02-13 Update eyeservosettings.h
    Re-calibrated the eyes.
2025-12-02 added armature dfx files
    [puppet_armature_back.dxf, puppet_armature_bottom.dxf, puppet_armature_handle.dxf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]
2025-12-28 head top
    [head top.3mf]
2025-12-28 speaker bracket
    [speaker_bracket.3mf]

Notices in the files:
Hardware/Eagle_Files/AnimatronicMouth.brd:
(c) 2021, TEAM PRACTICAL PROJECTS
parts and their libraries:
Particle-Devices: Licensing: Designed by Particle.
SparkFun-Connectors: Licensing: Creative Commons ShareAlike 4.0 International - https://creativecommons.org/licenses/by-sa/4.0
